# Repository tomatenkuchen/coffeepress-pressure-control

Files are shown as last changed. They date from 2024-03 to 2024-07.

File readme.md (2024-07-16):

# Embedded controller for coffee machine pressure control

My Pavoni Espresso Maker in their oldtimer form comes with limited and
inefficient steam pressure control
(litterally steam all you can, and vent the surplus away).
A power control via TRIAC and electronic pressure sensor can make a significant
difference on power intake and startup time.

Attention! This design involves dealing with high voltages that can be dealy of
lead to serious injury. Only qualified personel is allowed to assemble, test
and use these schematics. There's no warranity or responsibility from my
side, if things go wrong.

## documentation

all documentation is found in form of an [mdbook](https://rust-lang.github.io/mdBook/index.html).

## hardware

as this project is esp32 based, we need a pcb to mount the chip, the sensors
and the power stage. the pcb design and component simulation was made with
kicad 8.

## software

software is planned to be a rust embedded project.

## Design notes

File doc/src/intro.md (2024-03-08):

# La Pavoni pressre control project

projects aims are
- provide full digital pressure control via sensor and triac power control
- use electrical steam valve for milk skim and overpressure balance

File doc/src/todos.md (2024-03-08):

# Todos

- hardware
 - [ ] draw seeed chip layout
 - [ ] draw pcb for pavoni with hole in middle for fuse access
 - [ ] find pressure sensor
 - [ ] find steam valve
 - [ ] find cable system
- software
 - [ ] transpose software to seeed chip
 - [ ] test triac software
 - [ ] test adc input
 - [ ] write pressure control
 - [ ] write steam pressure critical handling
 - [ ] find interface via bluetooth or wifi

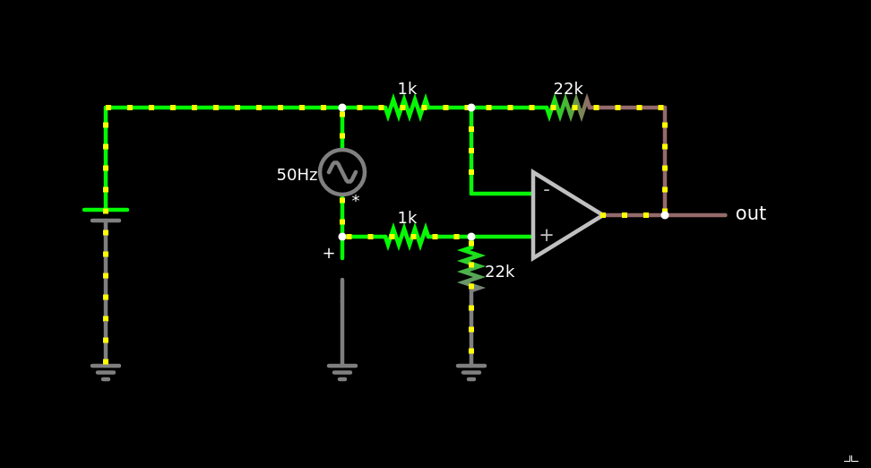
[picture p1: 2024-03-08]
hardware/docs/opv.png

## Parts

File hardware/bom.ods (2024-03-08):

Id | Designator | Package | Quantity | Designation | Supplier and ref
24 | BZ1 | Buzzer_15x7.5RM7.6 | 1 | Buzzer | x
6 | C1,C14 | CP_Radial_D8.0mm_P3.80mm | 2 | 2u2 | x
10 | C13 | C_Disc_D16.0mm_W5.0mm_P10.00mm | 1 | 10u | x
19 | C2 | CP_Radial_D5.0mm_P2.50mm | 1 | 4u7 | x
25 | C3 | CP_Radial_D8.0mm_P3.50mm | 1 | 470u | x
16 | C4 | CP_Radial_D8.0mm_P3.50mm | 1 | 220u | x
17 | C6 | CP_Radial_D4.0mm_P2.00mm | 1 | 470u | x
8 | D1 | D_A-405_P10.16mm_Horizontal | 1 | D | x
29 | D3,D2 | D_A-405_P10.16mm_Horizontal | 2 | UF4007 | x
9 | D6,D10,D7,D8,D9,D4,D5 | LED_D3.0mm | 7 | wt | x
23 | F1 | R_Axial_DIN0207_L6.3mm_D2.5mm_P15.24mm_Horizontal | 1 | 1.6A | x
21 | J1 | Molex_Micro-Latch_53254-0270_1x02_P2.00mm_Horizontal | 1 | Conn_01x02_Male | x
3 | J2,J3,J4 | TestPoint_Loop_D3.80mm_Drill2.8mm | 3 | Conn_01x01_Male | x
12 | J5 | PinHeader_1x04_P2.54mm_Vertical | 1 | Conn_01x04_Male | x
28 | L1 | L_Radial_D10.0mm_P5.00mm_Fastron_07P | 1 | 470u | x
14 | L2 | L_Axial_L7.0mm_D3.3mm_P12.70mm_Horizontal_Fastron_MICC | 1 | 2.2mH | x
11 | R1 | R_Axial_DIN0309_L9.0mm_D3.2mm_P15.24mm_Horizontal | 1 | 10 | x
30 | R2 | R_Axial_DIN0309_L9.0mm_D3.2mm_P12.70mm_Horizontal | 1 | 12k | x
32 | R32 | R_Axial_DIN0207_L6.3mm_D2.5mm_P10.16mm_Horizontal | 1 | 470 | x
7 | R35 | R_Axial_DIN0309_L9.0mm_D3.2mm_P12.70mm_Horizontal | 1 | 1k1 | x
13 | RV1 | RV_Disc_D12mm_W4.2mm_P7.5mm | 1 | 350V | x
22 | U1 | DIP-8_W7.62mm | 1 | h0536 | x
34 | U3 | ESP32-WROOM-32 | 1 | ESP32-WROOM-32 | x
5 | C9,C7,C6,C11,C10,C12,C8 | C_0603_1608Metric | 7 | 100n | conrad
33 | D11 | SOT-23 | 1 | BAT54SW | conrad
27 | Q1,Q3 | SOT-23 | 2 | BC848 | conrad
26 | Q2 | TO-220-3_Horizontal_TabDown | 1 | BTA16-600B | conrad
1 | R11,R56,R39,R16,R15,R17,R54,R43,R37,R13,R14,R55,R38,R51,R42,R12,R45,R31,R28,R30,R48,R47,R26,R29,R44,R49,R27,R46 | R_0603_1608Metric | 28 | 47k | conrad
18 | R34 | R_Axial_DIN0207_L6.3mm_D2.5mm_P10.16mm_Horizontal | 1 | 100 | x
20 | R36 | R_2512_6332Metric | 1 | 0R01 | conrad
2 | R41,R10,R3,R18,R33,R22,R40,R6,R52,R5,R53,R24,R9,R21,R4,R7,R25,R23,R19,R20,R8,R50 | R_0603_1608Metric | 22 | 4k7 | conrad
4 | SW7,SW1,SW2,SW4,SW6,SW5,SW3 | SW_PUSH_6mm | 7 | SW_Push | conrad
31 | U2 | SOT-223-3_TabPin2 | 1 | LD1117S33TR_SOT223 | conrad
15 | U4 | SO-8_5.3x6.2mm_P1.27mm | 1 | TL082 | conrad

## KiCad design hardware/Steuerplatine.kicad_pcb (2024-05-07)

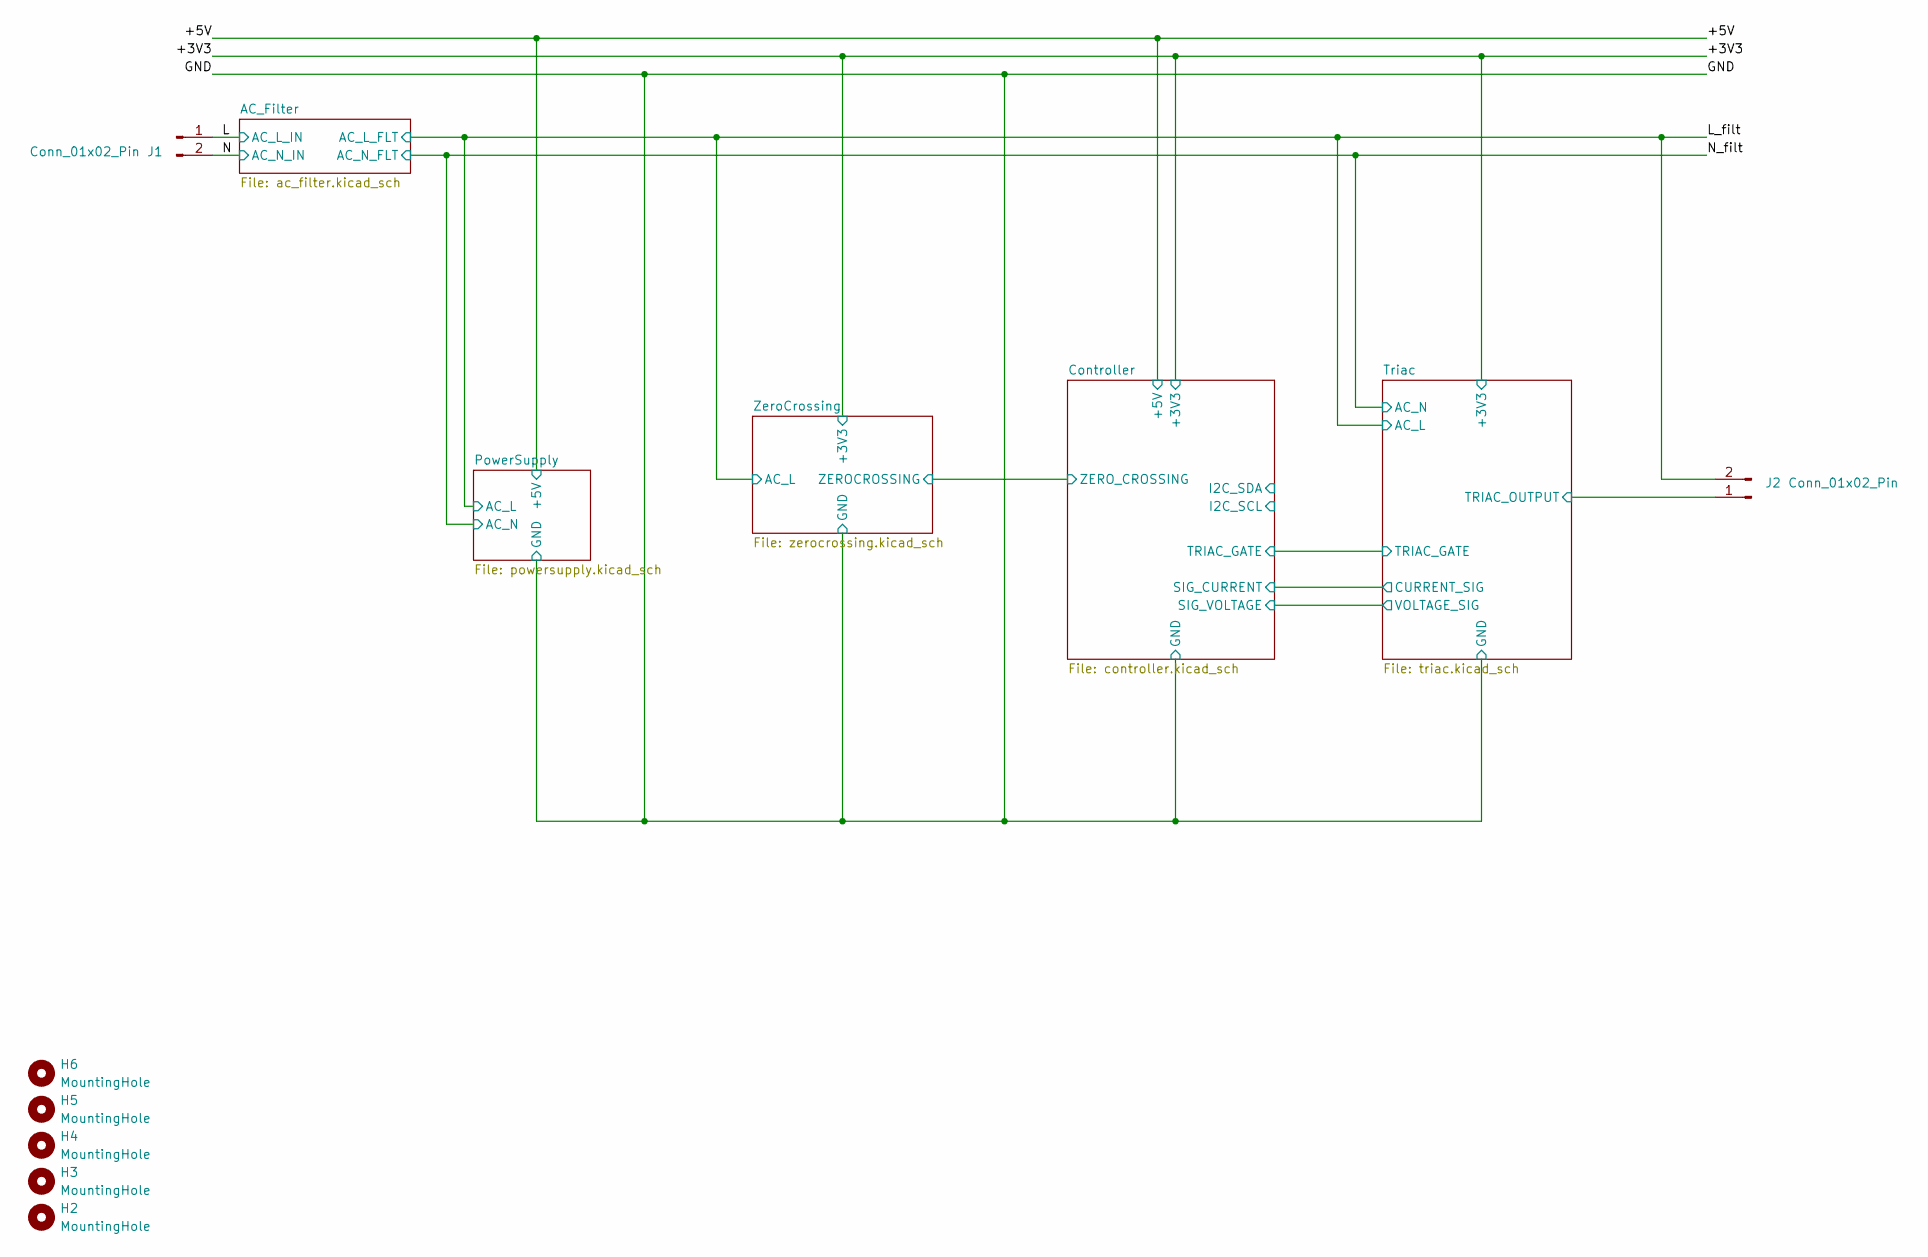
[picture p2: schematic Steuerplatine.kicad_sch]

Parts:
H2, H3, H4, H5, H6: MountingHole; MountingHole_3.5mm
J1, J2: Conn_01x02_Pin; PhoenixContact_MSTBA_2,5_2-G_1x02_P5.00mm_Horizontal

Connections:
/L: J1.1, J2.2; also elsewhere on the board
/N: J1.2; also elsewhere on the board
/Triac/TRIAC_OUTPUT: J2.1; also elsewhere on the board

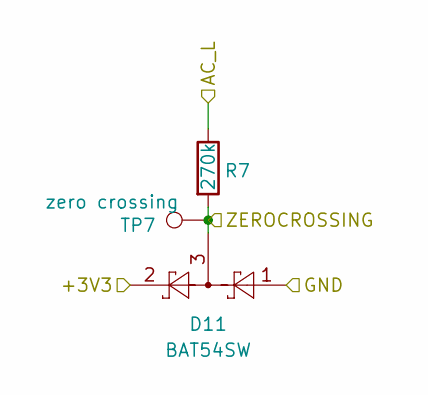
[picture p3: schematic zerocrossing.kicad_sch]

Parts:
D11: BAT54SW; SOT-23
R7: 270k; R_MELF_MMB-0207
TP7: zero crossing; TestPoint_Pad_D1.0mm

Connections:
/+3V3: D11.2; also elsewhere on the board
/Controller/ZERO_CROSSING: D11.3, R7.2, TP7.1; also elsewhere on the board
/GND: D11.1; also elsewhere on the board
/L: R7.1; also elsewhere on the board

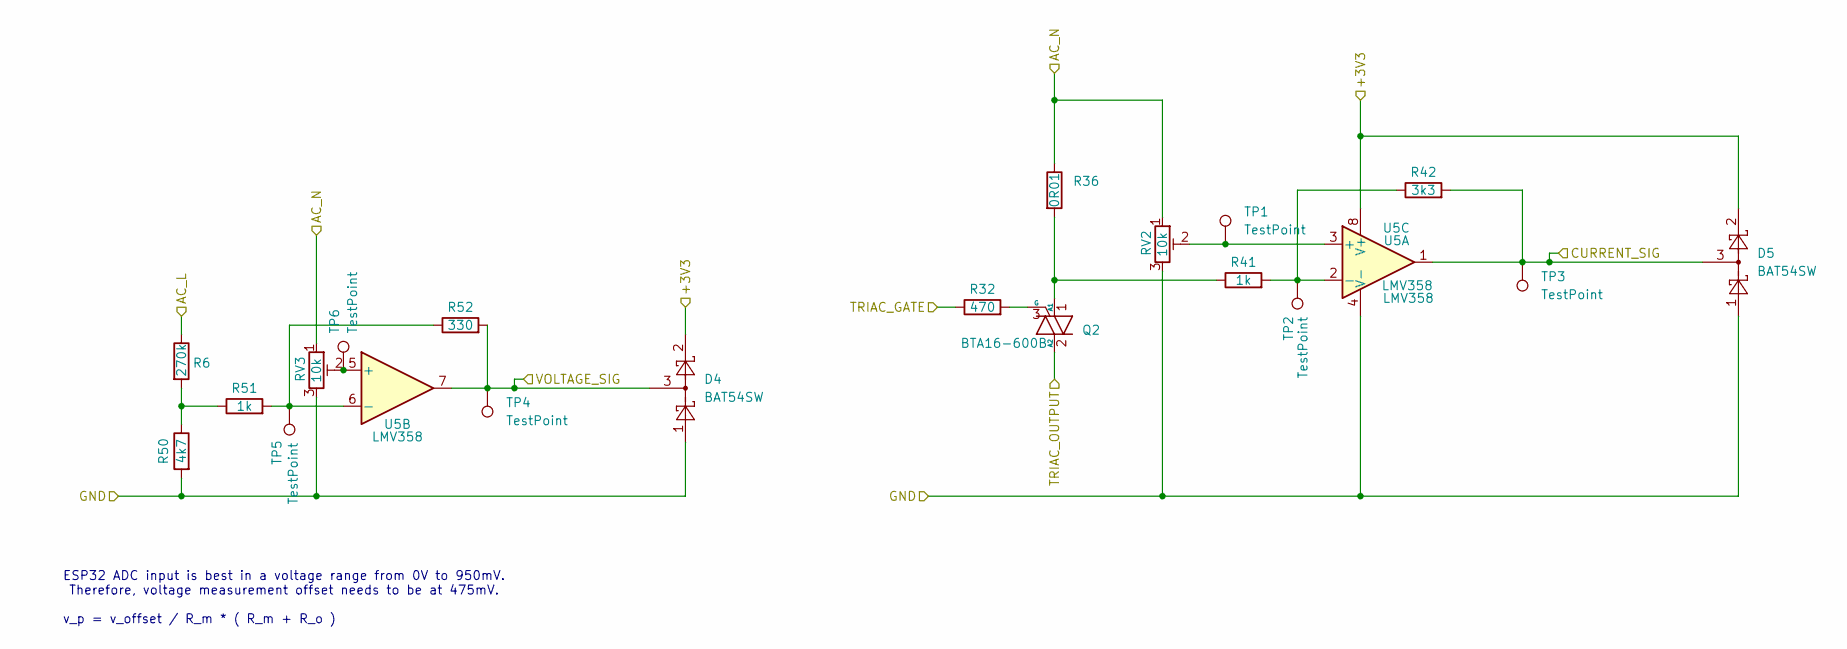
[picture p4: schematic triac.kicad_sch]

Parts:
D4, D5: BAT54SW; SOT-23
Q2: BTA16-600B; TO-220-3_Horizontal_TabDown
R6: 270k; R_MELF_MMB-0207
R32: 470; R_0603_1608Metric
R36: 0R01; R_2512_6332Metric
R41, R51: 1k; R_0603_1608Metric
R42: 3k3; R_0603_1608Metric
R50: 4k7; R_0603_1608Metric
R52: 330; R_0603_1608Metric
RV2, RV3: 10k; Potentiometer_Bourns_3299W_Vertical
TP1, TP2, TP3, TP4, TP5, TP6: TestPoint; TestPoint_Pad_D1.0mm
U5: LMV358; SOIC-8_3.9x4.9mm_P1.27mm

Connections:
/+3V3: D4.2, D5.2, U5.8 (V+); also elsewhere on the board
/Controller/SIG_CURRENT: D5.3, R42.2, TP3.1, U5.1; also elsewhere on the board
/Controller/SIG_VOLTAGE: D4.3, R52.2, TP4.1, U5.7; also elsewhere on the board
/Controller/TRIAC_GATE: R32.1; also elsewhere on the board
/GND: D4.1, D5.1, R50.2, RV2.3, RV3.3, U5.4 (V-); also elsewhere on the board
/L: R6.1; also elsewhere on the board
/N_filt: R36.1, RV2.1, RV3.1; also elsewhere on the board
/Triac/TRIAC_OUTPUT: Q2.2 (A2); also elsewhere on the board
unnamed: Q2.1 (A1), R36.2, R41.1
unnamed: Q2.3 (G), R32.2
unnamed: R6.2, R50.1, R51.1
unnamed: RV2.2, TP1.1, U5.3 (+)
unnamed: R41.2, R42.1, TP2.1, U5.2 (-)
unnamed: RV3.2, TP6.1, U5.5 (+)
unnamed: R51.2, R52.1, TP5.1, U5.6 (-)

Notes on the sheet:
ESP32 ADC input is best in a voltage range from 0V to 950mV. Therefore, voltage measurement offset needs to be at 475mV.
v_p = v_offset / R_m * ( R_m + R_o )

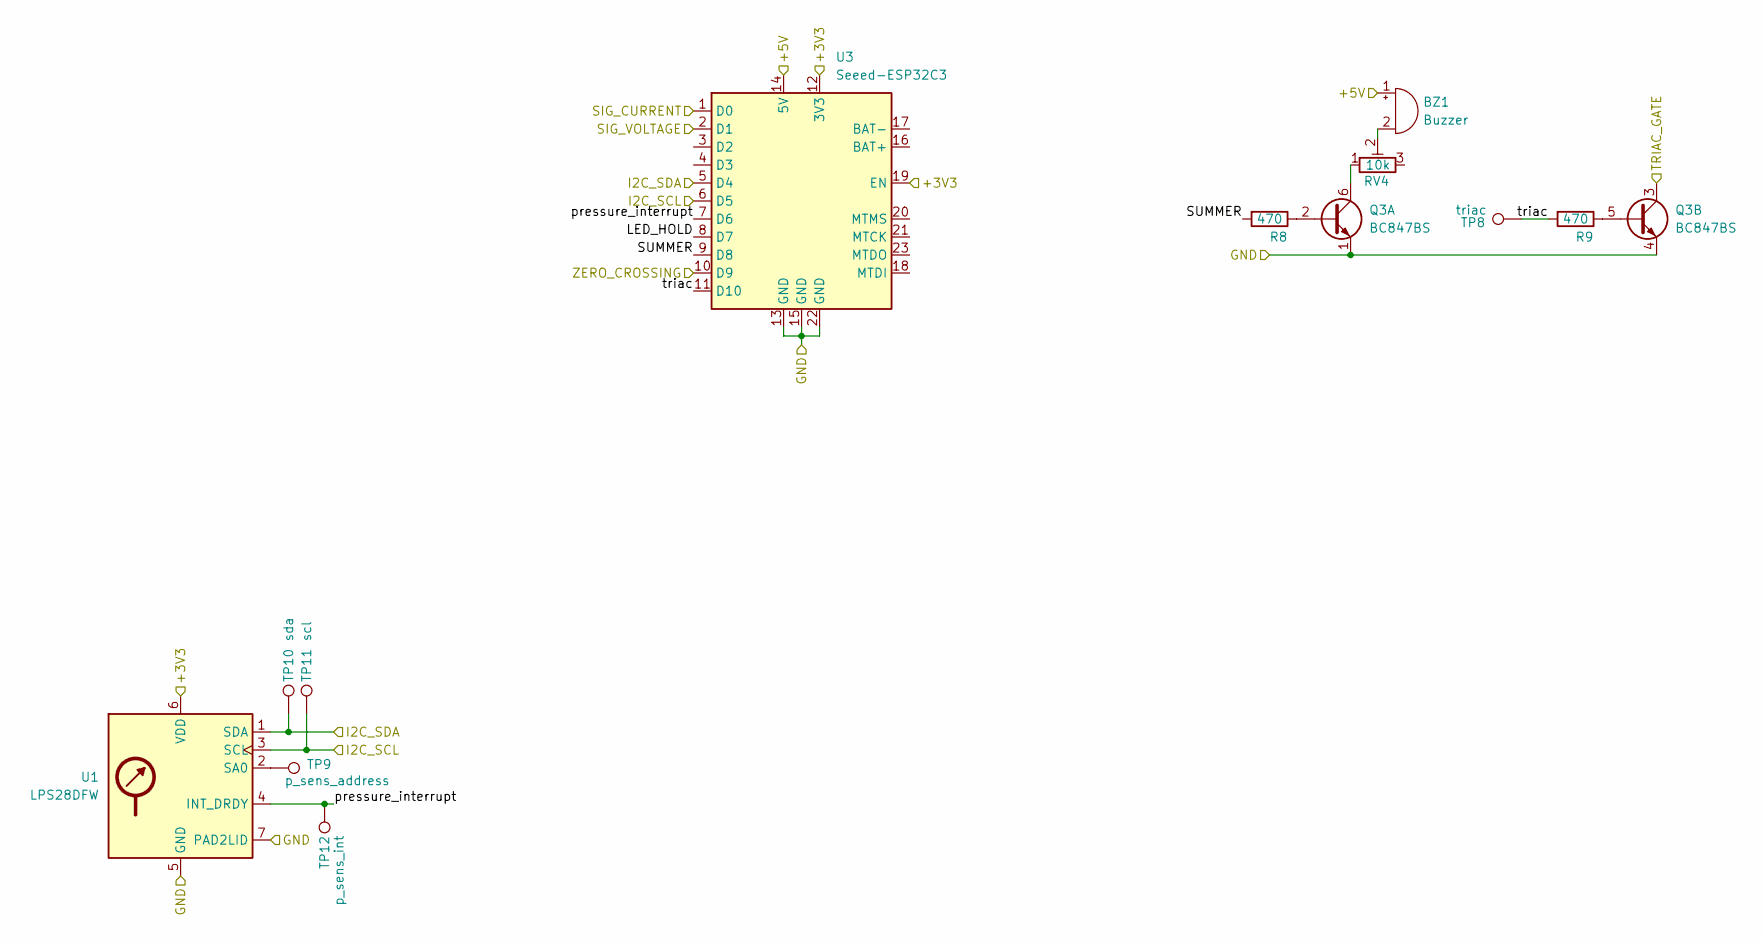
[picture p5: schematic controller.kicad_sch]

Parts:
BZ1: Buzzer; Buzzer_15x7.5RM7.6
Q3: BC847BS; SOT-363_SC-70-6
R8, R9: 470; R_0603_1608Metric
RV4: 10k; Potentiometer_Bourns_3299W_Vertical
TP8: triac; TestPoint_Pad_D1.0mm
TP9: p_sens_address; TestPoint_Pad_D1.0mm
TP10: sda; TestPoint_Pad_D1.0mm
TP11: scl; TestPoint_Pad_D1.0mm
TP12: p_sens_int; TestPoint_Pad_D1.0mm
U1: LPS28DFW; ST_LPS28DFW
U3: Seeed-ESP32C3; MCU_Seeed_ESP32C3

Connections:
/+3V3: U1.6 (VDD), U3.12 (3V3), U3.19 (EN); also elsewhere on the board
/+5V: BZ1.1 (-), U3.14 (5V); also elsewhere on the board
/Controller/I2C_SCL: TP11.1, U1.3 (SCL), U3.6 (D5)
/Controller/I2C_SDA: TP10.1, U1.1 (SDA), U3.5 (D4)
/Controller/LED_HOLD: U3.8 (D7)
/Controller/SIG_CURRENT: U3.1 (D0); also elsewhere on the board
/Controller/SIG_VOLTAGE: U3.2 (D1); also elsewhere on the board
/Controller/SUMMER: R8.2, U3.9 (D8)
/Controller/TRIAC_GATE: Q3.3 (C2); also elsewhere on the board
/Controller/ZERO_CROSSING: U3.10 (D9); also elsewhere on the board
/Controller/pressure_interrupt: TP12.1, U1.4 (INT_DRDY), U3.7 (D6)
/Controller/triac: R9.2, TP8.1, U3.11 (D10)
/GND: Q3.1 (E1), Q3.4 (E2), U1.5 (GND), U1.7 (PAD2LID), U3.13 (GND), U3.15 (GND), U3.22 (GND); also elsewhere on the board
unnamed: BZ1.2 (+), RV4.2
unnamed: Q3.2 (B1), R8.1
unnamed: Q3.6 (C1), RV4.1
unnamed: Q3.5 (B2), R9.1
unnamed: TP9.1, U1.2 (SA0)

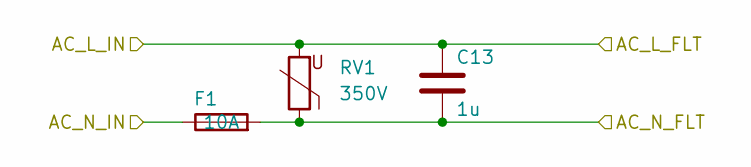
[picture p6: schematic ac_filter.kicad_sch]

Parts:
C13: 1u; C_Rect_L18.0mm_W8.0mm_P15.00mm_FKS3_FKP3
F1: 10A; Fuseholder_Clip-5x20mm_Schurter_CQM_Inline_P20.60x5.00mm_D1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
RV1: 350V; RV_Disc_D12mm_W4.2mm_P7.5mm

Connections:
/L: C13.1, RV1.2; also elsewhere on the board
/N: F1.1; also elsewhere on the board
/N_filt: C13.2, F1.2, RV1.1; also elsewhere on the board

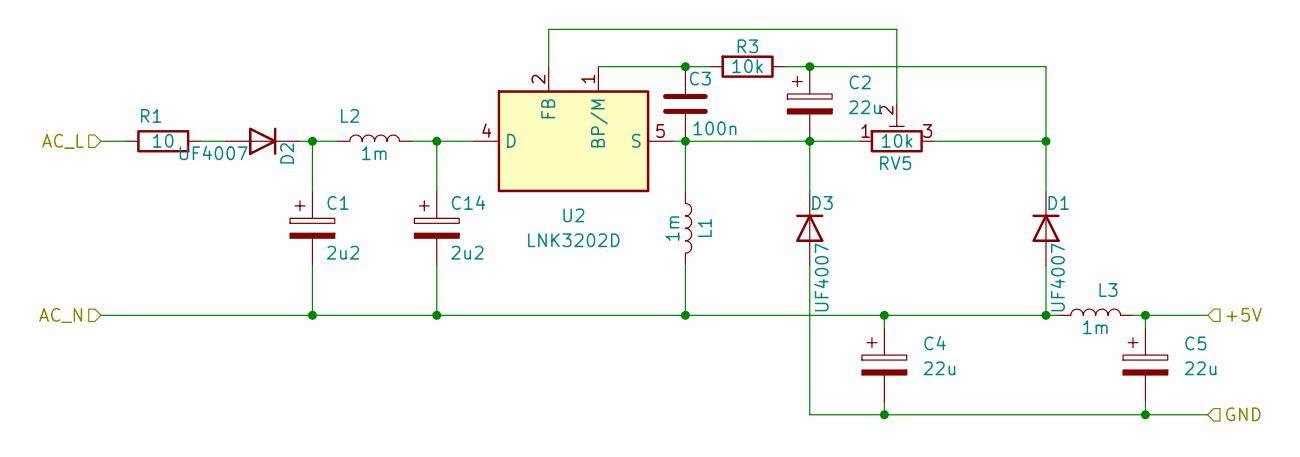
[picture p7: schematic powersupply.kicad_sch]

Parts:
C1, C14: 2u2; CP_Elec_8x10
C2, C4, C5: 22u; CP_Elec_6.3x3
C3: 100n; C_0603_1608Metric
D1, D2, D3: UF4007; D_SMB
L1, L2, L3: 1m; L_Wuerth_WE-XHMI-8080
R1: 10; R_2816_7142Metric
R3: 10k; R_0603_1608Metric
RV5: 10k; Potentiometer_Bourns_3299W_Vertical
U2: LNK3202D; PowerIntegrations_SO-8C

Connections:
/+5V: C5.1, L3.2; also elsewhere on the board
/GND: C4.2, C5.2, D3.2 (A); also elsewhere on the board
/L: R1.1; also elsewhere on the board
/N_filt: C1.2, C4.1, C14.2, D1.2 (A), L1.2, L3.1; also elsewhere on the board
unnamed: C2.1, D1.1 (K), R3.1, RV5.3
unnamed: D2.2 (A), R1.2
unnamed: C1.1, D2.1 (K), L2.1
unnamed: C2.2, C3.1, D3.1 (K), L1.1, RV5.1, U2.5 (S), U2.6 (S), U2.7 (S), U2.8 (S)
unnamed: C3.2, R3.2, U2.1 (BP/M)
unnamed: C14.1, L2.2, U2.4 (D)
unnamed: RV5.2, U2.2 (FB)

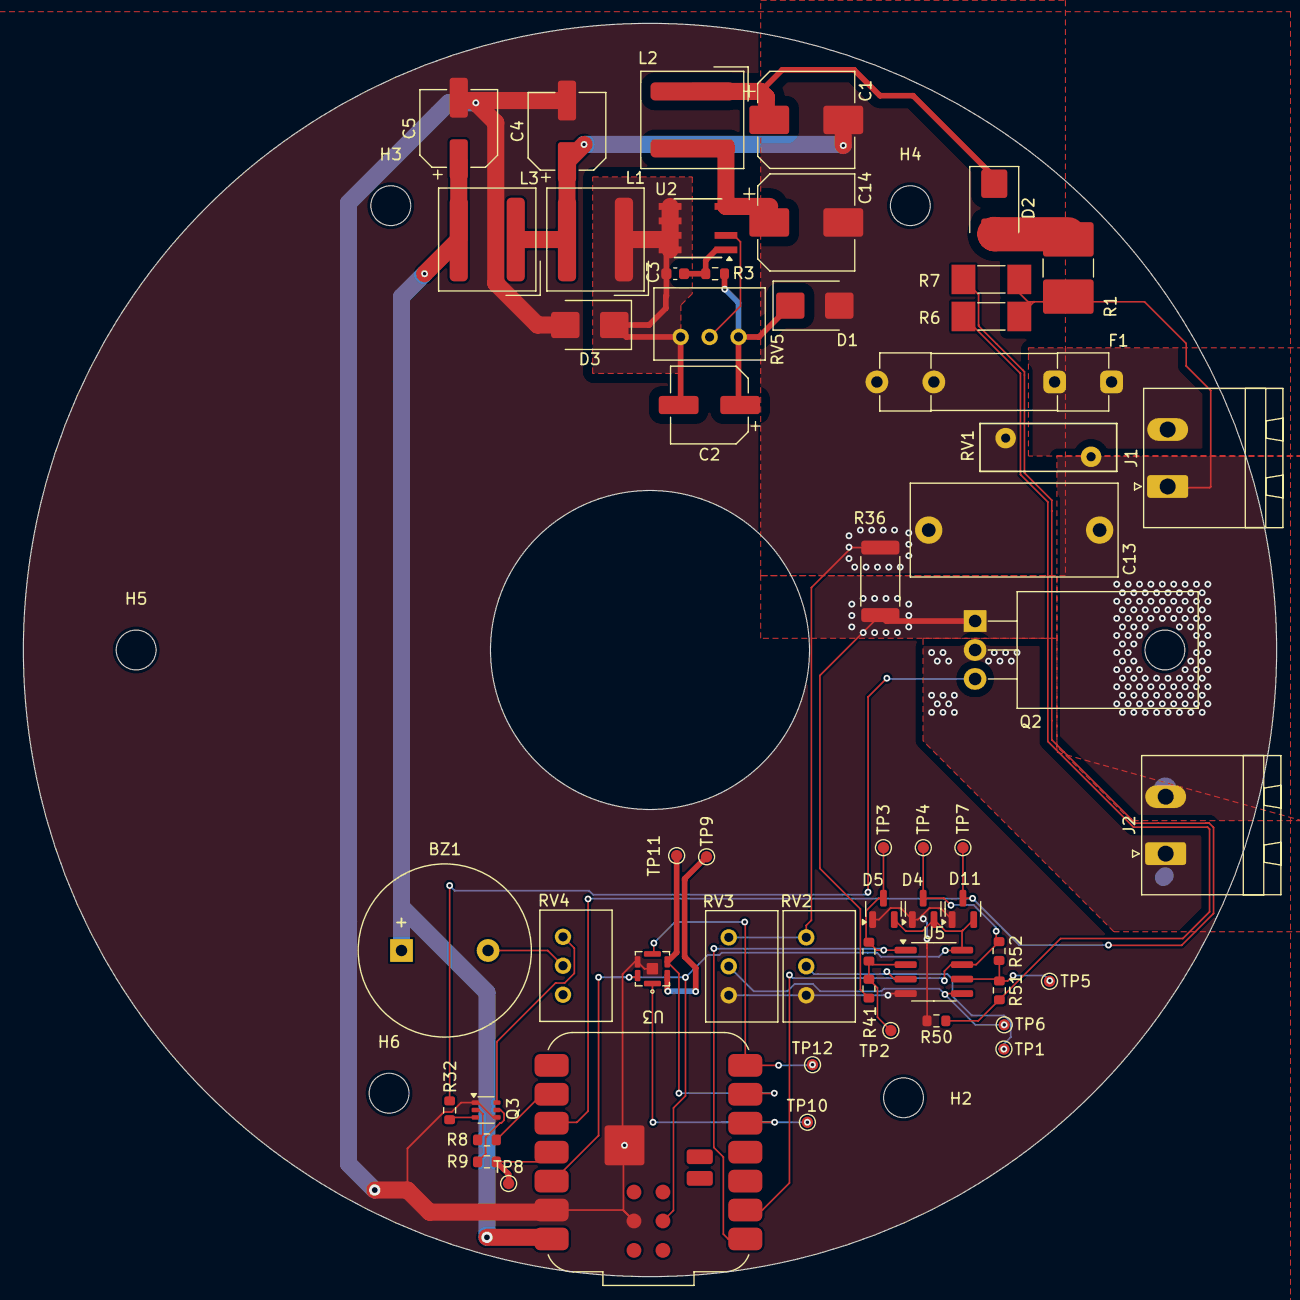
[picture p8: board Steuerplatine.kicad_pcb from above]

Board: 2 copper layers, 110.0 x 110.0 mm, 61 parts (0 on the bottom side), 35 nets.

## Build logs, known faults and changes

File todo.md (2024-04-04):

# todo

## hardware
- [x] adapted opamps
- [x] add kicad footprint lib: seeed xiao esp32-c3
- [x] add kicad symbol lib: seeed xiao esp32-c3
- [x] update 5V source
- [x] update layout
- [ ] add wifi
- [x] add pressure sensor
- [ ] add steam vent
- [x] route hardware
- [x] find interface for pressure sensor

## software
- [x] setup chip tools
- [ ] create phase cut
- [ ] create pressure sensor
- [ ] create power analyzer
- [ ] order
- [ ] build
- [ ] test

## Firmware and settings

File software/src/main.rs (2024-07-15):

#![no_std]
#![no_main]

extern crate lps28dfw;

use esp_backtrace as _;
use esp_hal::{
    analog::adc::{AdcConfig, Attenuation, Adc},
    clock::ClockControl,
    delay::Delay,
    gpio::Io,
    i2c::I2C,
    peripherals::Peripherals,
    prelude::*,
    system::SystemControl,
};
use esp_println::println;

#[entry]
fn main() -> ! {
    // init peripherals access point
    let peripherals = Peripherals::take();
    // init system
    let system = SystemControl::new(peripherals.SYSTEM);
    // init clock
    let clocks = ClockControl::boot_defaults(system.clock_control).freeze();

    let io = Io::new(peripherals.GPIO, peripherals.IO_MUX);
    let i2c_sda_pin = io.pins.gpio4;
    let i2c_scl_pin = io.pins.gpio5;

    // enable i2c for pressure sensor
    let i2c = I2C::new(
        peripherals.I2C0,
        i2c_sda_pin,
        i2c_scl_pin,
        100u32.kHz(),
        &clocks,
        None,
    );

    // set up pressure sensor
    let mut p_sens = lps28dfw::LPS28DFW::new(i2c, lps28dfw::I2CAddress::Low, lps28dfw::Range::Range4060hPa);
    // check if pressure sensor is alive
    p_sens.identify().unwrap();

    // get grid voltage input
    let mut adc1_config = AdcConfig::new();
    let mut adc_input_heater_current = adc1_config.enable_pin(io.pins.gpio0, Attenuation::Attenuation11dB);
    let mut adc_input_grid_voltage = adc1_config.enable_pin(io.pins.gpio1, Attenuation::Attenuation11dB);
    let mut adc1 = Adc::new(peripherals.ADC1, adc1_config);

    let delay = Delay::new(&clocks);

    loop {
        // read adc
        let i_grid_value: u16 = nb::block!(adc1.read_oneshot(&mut adc_input_heater_current)).unwrap();
        let v_grid_value: u16 = nb::block!(adc1.read_oneshot(&mut adc_input_grid_voltage)).unwrap();

        // read pressure sensor
        let p = p_sens.read_pressure().unwrap();
        println!("ADC1: v_grid = {}, i_grid = {}",v_grid_value, i_grid_value);
        println!("I2C0 : data array = {:?}", p);
        delay.delay_millis(2000u32);
    }
}

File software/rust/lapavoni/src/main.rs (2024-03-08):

#![no_std]
#![no_main]

use esp32c3_hal::{clock::ClockControl, peripherals::Peripherals, prelude::*, Delay};
use esp_backtrace as _;
use esp_println::println;

#[entry]
fn main() -> ! {
    let peripherals = Peripherals::take();
    let system = peripherals.SYSTEM.split();

    let clocks = ClockControl::max(system.clock_control).freeze();
    let mut delay = Delay::new(&clocks);

    println!("Hello world!");
    loop {
        println!("Loop...");
        delay.delay_ms(500u32);
    }
}

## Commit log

2024-03-20 done routing
    [Steuerplatine.kicad_pcb, Steuerplatine.kicad_sch, ac_filter.kicad_sch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]
2024-03-23 added pressure sensor
    [Steuerplatine.kicad_pcb, Steuerplatine.kicad_sch, controller.kicad_sch]
2024-03-29 bugfix: triac output needs to confront L potential
    [Steuerplatine.kicad_pcb, Steuerplatine.kicad_sch, ac_filter.kicad_sch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]
2024-03-30 added some zones
    [Steuerplatine.kicad_pcb, Steuerplatine.kicad_sch, ac_filter.kicad_sch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]
2024-03-31 added some datasheets
    [Steuerplatine.kicad_pcb, ac_filter.kicad_sch, controller.kicad_sch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]
2024-03-31 ignore bom
2024-03-31 some more rules and routings
    [Steuerplatine.kicad_pcb, Steuerplatine.kicad_sch, controller.kicad_sch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]
2024-03-31 changed capacitors to smd
    [controller.kicad_sch, powersupply.kicad_sch]
2024-03-31 changed diodes footprint
    [powersupply.kicad_sch]
2024-03-31 added gnd layer
    [Steuerplatine.kicad_pcb, Steuerplatine.kicad_sch, triac.kicad_sch]
2024-04-01 restructured copper planes
    [Steuerplatine.kicad_pcb, ac_filter.kicad_sch]
2024-04-01 changed some parts to stuff you can actually order
    [Steuerplatine.kicad_pcb, powersupply.kicad_sch]
2024-04-01 added testpoints. adjusted opamps for correct measurement. replaced hard resistors with potentiometer trimmers if necessary
    [Steuerplatine.kicad_pcb, controller.kicad_sch, powersupply.kicad_sch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]
2024-05-07 changed opamp for a rail-to-rail device. bugfix: got the right package for phoenix mstba outlets. beauty: rearranged some test points for better visibility. bugfix: added bypass diodes to analog outp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
    [Steuerplatine.kicad_pcb, Steuerplatine.kicad_sch, ac_filter.kicad_sch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]
2024-05-12 got a first running software for adc access
2024-05-18 added voltage adc input
2024-05-18 added i2c
2024-05-20 added identity request on i2c
2024-07-07 changed i2c request to sensor request
2024-07-15 updated pressure sensor driver to a nostd friendly version.
    updated main to esp-hal 0.18.0 standart
2024-07-16 updated to more modern esp32 template. added wifi modules
2024-07-16 removed la pavoni from title
